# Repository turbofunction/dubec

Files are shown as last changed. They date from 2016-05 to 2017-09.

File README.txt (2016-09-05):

Contact:
Janne Savukoski
<firstname>@savukoski.name

                    Part name: DUBEC
                     Revision: 2.3
                   Board size: 40mm x 21.375mm
              Board thickness: 
                   Board type: Four layer
       Outer copper thickness:
       Inner copper thickness:
Solder mask color (top & bot):
 Silkscreen color (top & bot):

No special instructions.

Layer order:

TOP:    DUBEC.toplayer.ger
        DUBEC.internalplane1.ger
        DUBEC.internalplane2.ger
BOTTOM: DUBEC.bottomlayer.ger

Other files:

DUBEC.boardoutline.ger     Outline
DUBEC.topsoldermask.ger    Solder mask TOP
DUBEC.bottomsoldermask.ger Solder mask BOTTOM
DUBEC.topsilkscreen.ger    Silkscreen TOP
DUBEC.bottomsilkscreen.ger Silkscreen BOTTOM
DUBEC.drills.xln           Excellon drill
DUBEC.drl                  Drill rack
DUBEC.tcream.ger           Solder stencil (TOP)

Thank you!

Regards,
Janne Savukoski

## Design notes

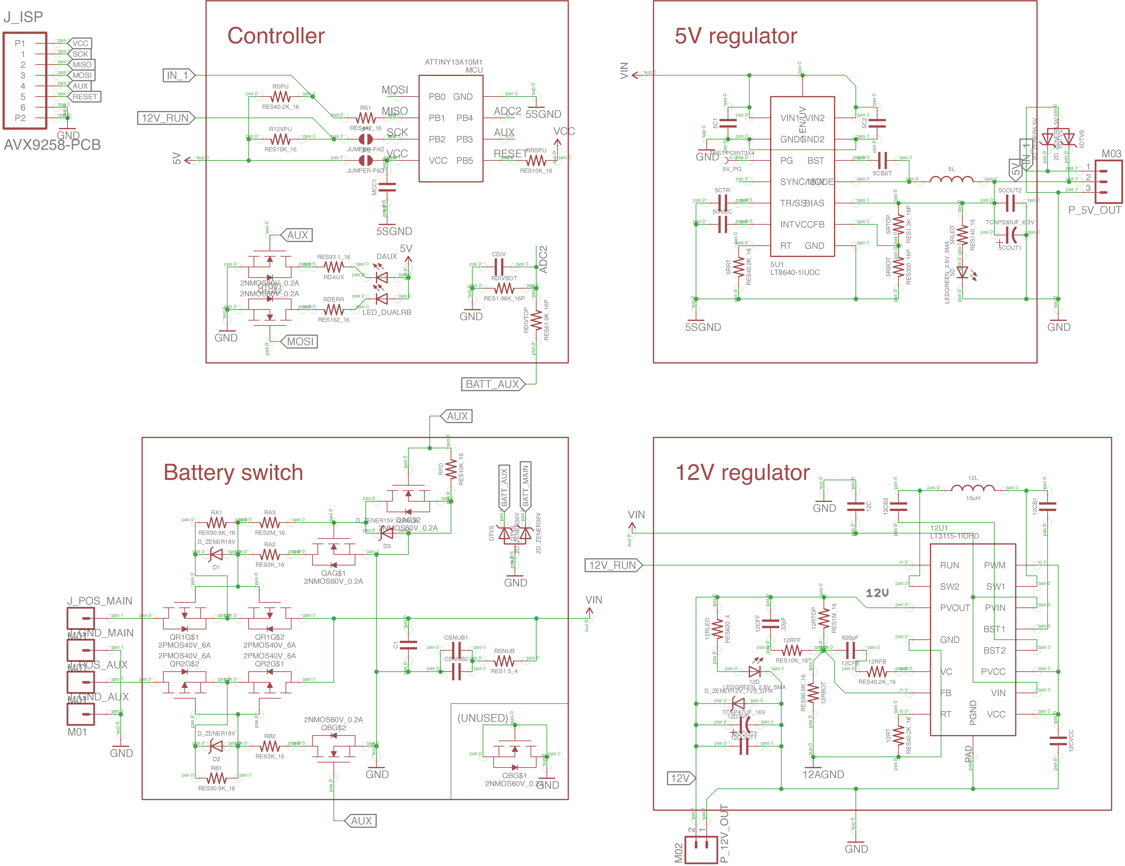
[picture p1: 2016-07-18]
DUBEC-schema-v2_0.png

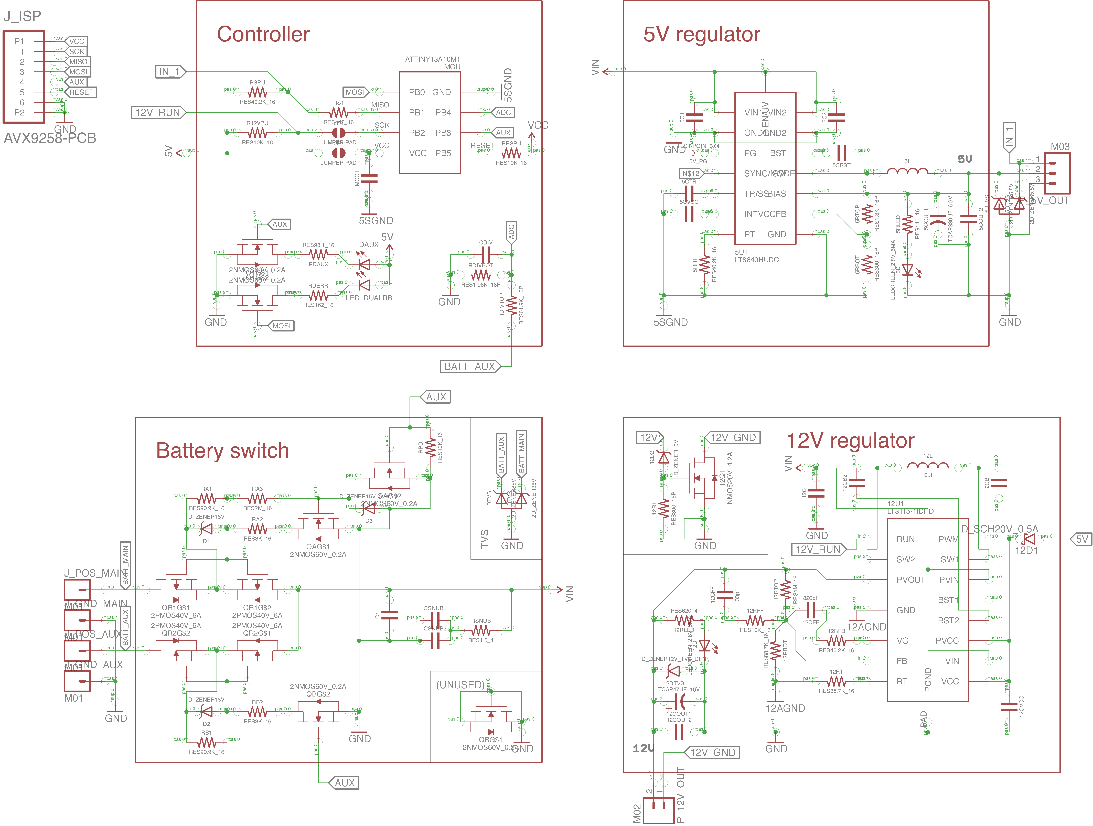
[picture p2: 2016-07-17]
DUBEC-schema.png

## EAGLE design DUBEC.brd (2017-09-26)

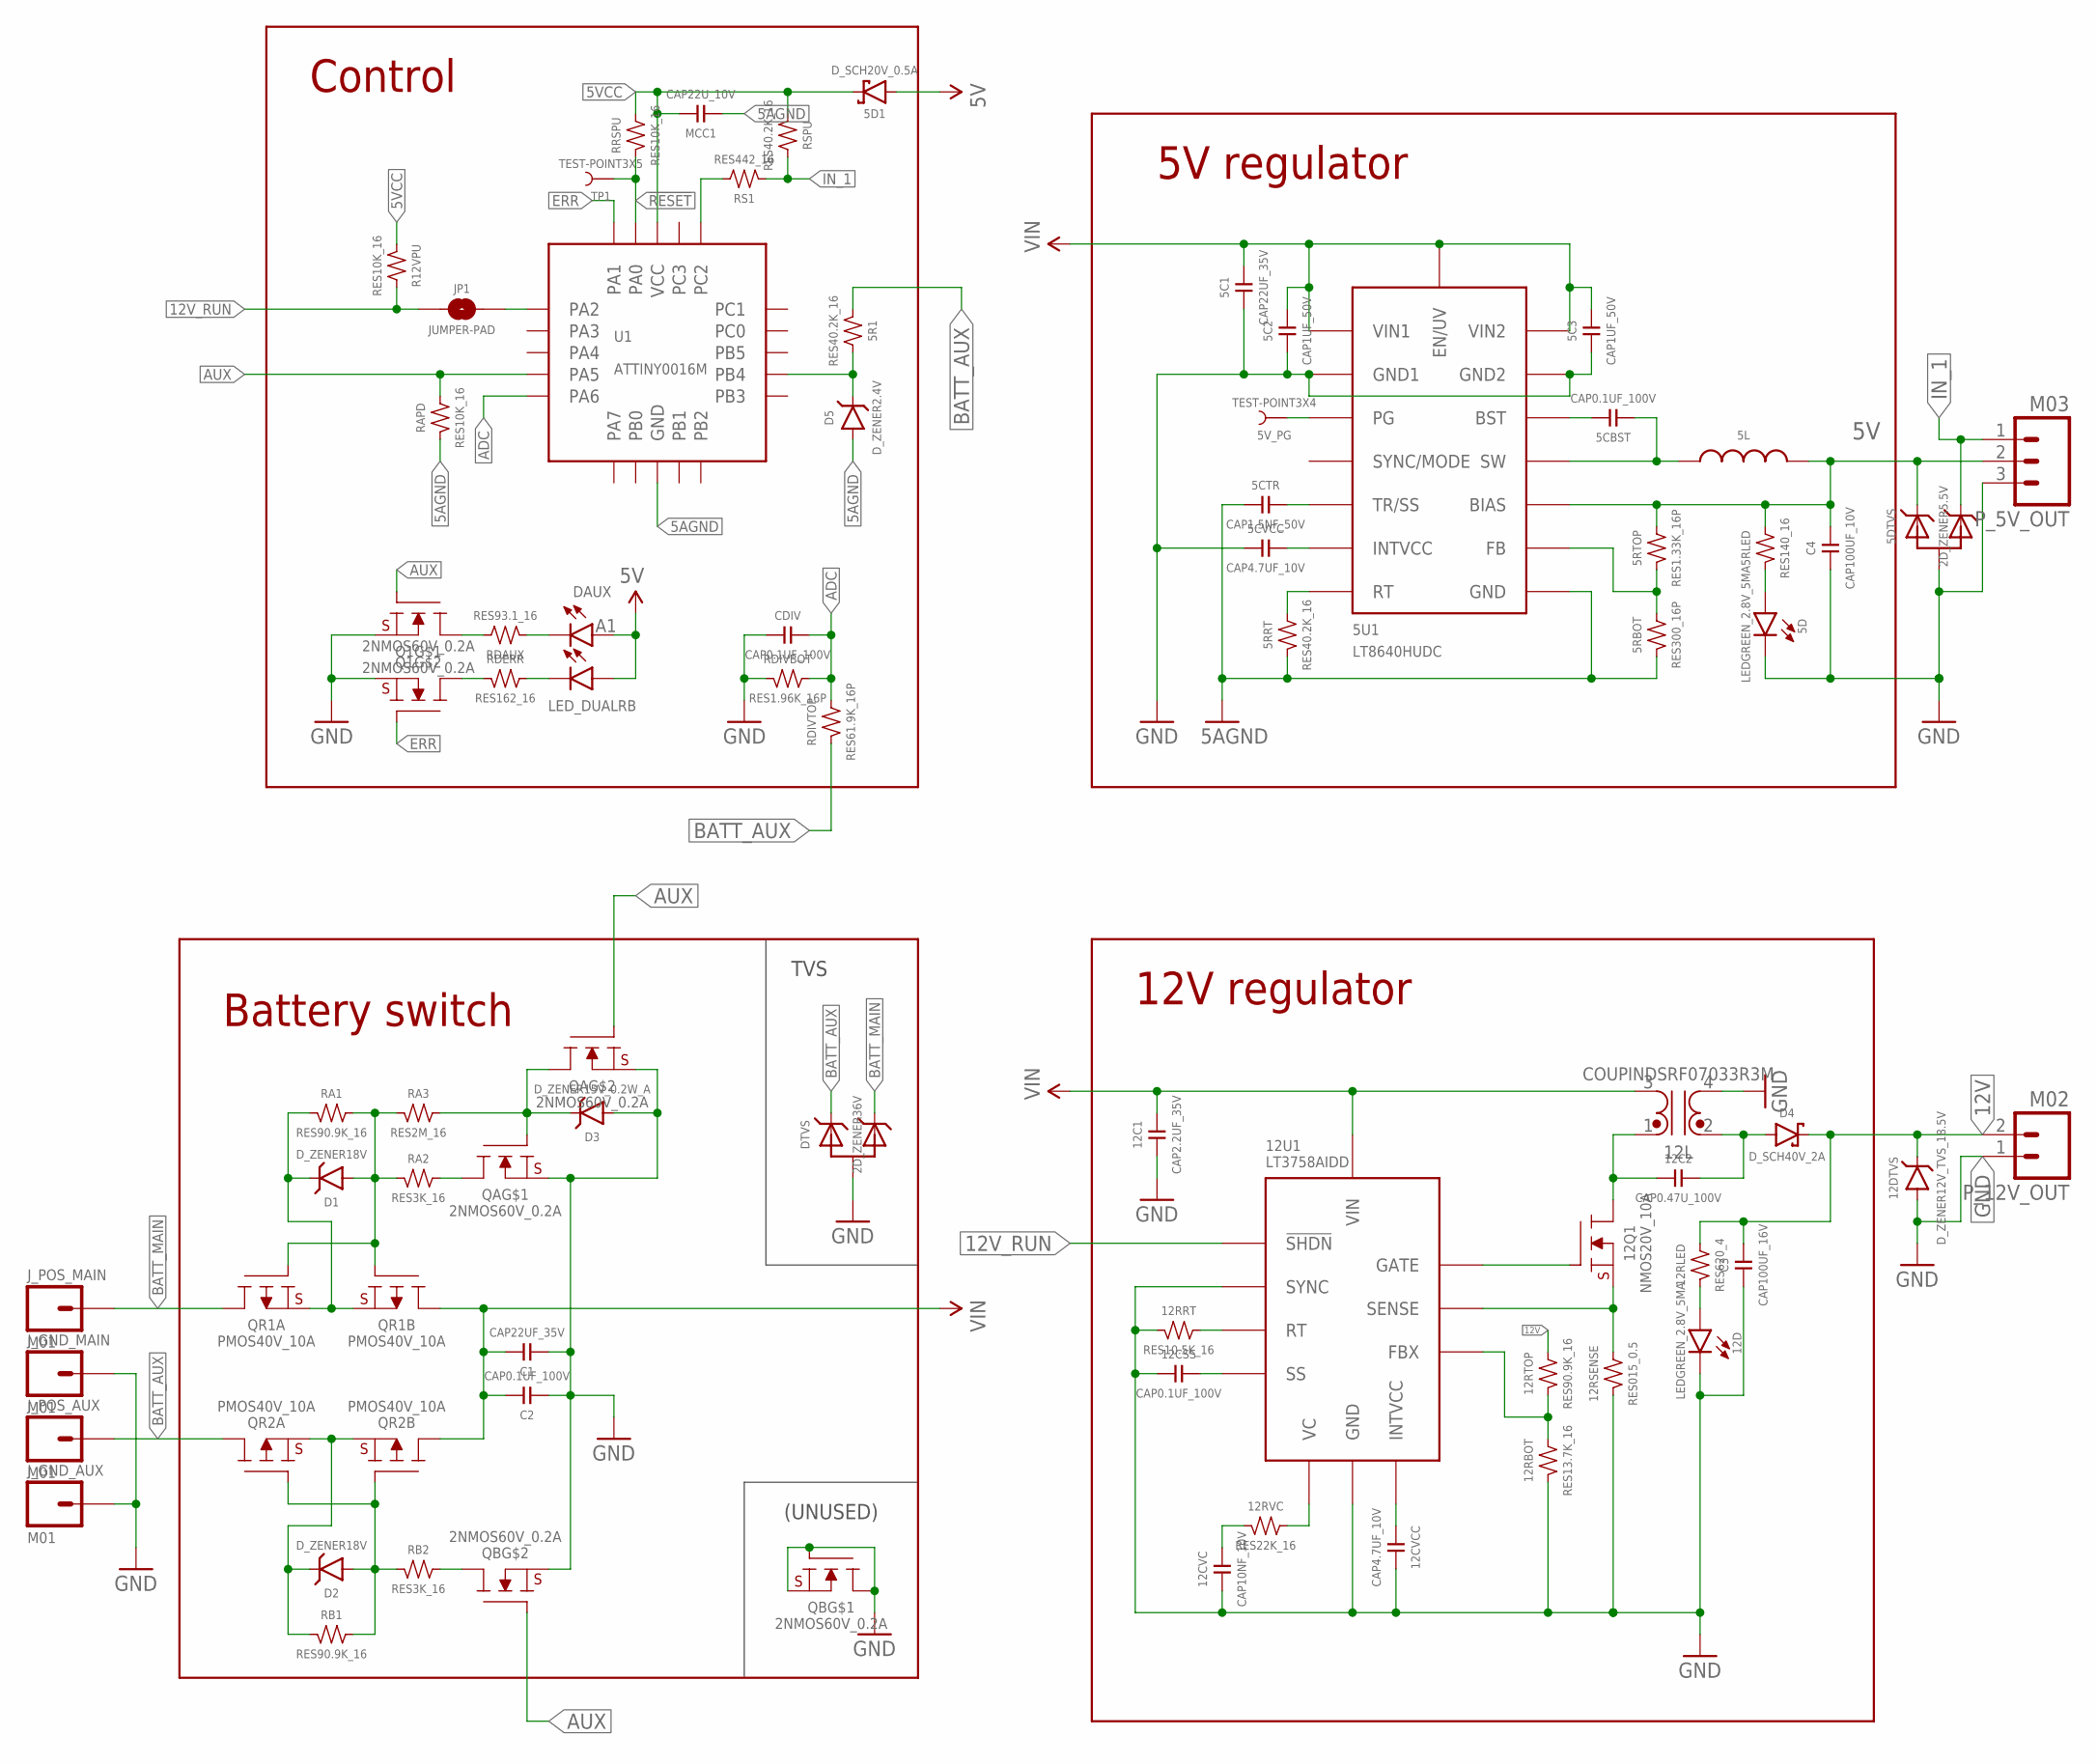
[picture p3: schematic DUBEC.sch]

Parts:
5C1: CAP22UF_35V; 0805
5C2, 5C3: CAP1UF_50V; 0603
5CBST, 12CSS: CAP0.1UF_100V; 0402
5CTR: CAP1.5NF_50V; 0402
5CVCC, 12CVCC: CAP4.7UF_10V; 0402
5D, 12D: LEDGREEN_2.8V_5MA; 0603+
5D1: D_SCH20V_0.5A; SOD523+
5DTVS: 2D_ZENER5.5V; SOT23-3
5L: I3.3UH_5A; SRP5030
5R1, 5RRT: RES40.2K_16; 0402
5RBOT: RES300_16P; 0402
5RLED: RES140_16; 0402
5RTOP: RES1.33K_16P; 0402
5U1: LT8640HUDC; QFN-18
5V_PG: TEST-POINT3X4; PAD.03X.04
12C1: CAP2.2UF_35V; 0402
12C2: CAP0.47U_100V; 0805
12CVC: CAP10NF_10V; 0402
12DTVS: D_ZENER12V_TVS_18.5V; SOD323+
12L: COUPINDSRF07033R3M; SRF0703
12Q1: NMOS20V_10A; 6-PQFN
12RBOT: RES13.7K_16; 0402
12RLED: RES620_4; 0603
12RRT: RES10.5K_16; 0402
12RSENSE: RES015_0.5; 1206
12RTOP: RES90.9K_16; 0402
12RVC: RES22K_16; 0402
12U1: LT3758AIDD; DFN-10
C1: CAP22UF_35V; 0805
C2: CAP0.1UF_100V; 0402
C3: CAP100UF_16V; 1210
C4: CAP100UF_10V; 1210
CDIV: CAP0.1UF_100V; 0402
D1, D2: D_ZENER18V; SOD523+
D3: D_ZENER15V_0.2W_A; SOD523+
D4: D_SCH40V_2A; DO-214AC
D5: D_ZENER2.4V; SOD523+
DAUX: LED_DUALRB; 0603+DUAL
DTVS: 2D_ZENER36V; SOT23-3
JP1: JUMPER-PAD; JUMPER-PAD-ROUND
J_GND_AUX: M01; 1X01_NO_SILK
J_GND_MAIN: M01; 1X01_NO_SILK
J_POS_AUX: M01; 1X01_NO_SILK
J_POS_MAIN: M01; 1X01_NO_SILK
MCC1: CAP22U_10V; 0603
P_5V_OUT: M03; 1X03_NO_SILK
P_12V_OUT: M02; 1X02_NO_SILK
Q1: 2NMOS60V_0.2A; SOT-666
QA: 2NMOS60V_0.2A; SOT-666
QB: 2NMOS60V_0.2A; SOT-666
QR1A, QR1B, QR2A, QR2B: PMOS40V_10A; POWERDI3333-8
R12VPU: RES10K_16; 0402
RA1: RES90.9K_16; 0402
RA2: RES3K_16; 0402
RA3: RES2M_16; 0402
RAPD: RES10K_16; 0402
RB1: RES90.9K_16; 0402
RB2: RES3K_16; 0402
RDAUX: RES93.1_16; 0402
RDERR: RES162_16; 0402
RDIVBOT: RES1.96K_16P; 0402
RDIVTOP: RES61.9K_16P; 0402
RRSPU: RES10K_16; 0402
RS1: RES442_16; 0402
RSPU: RES40.2K_16; 0402
TP1: TEST-POINT3X5; PAD.03X.05
U1: ATTINY0016M; 20-VQFN-2

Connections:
5AGND: 5CTR.1, 5RBOT.1, 5RRT.1, 5U1.18 (GND), D5.A, MCC1.1, RAPD.1, U1.3 (GND), U1.PAD (GND)
5V: 5D1.A, 5DTVS.1 (C1), 5L.2, 5RLED.2, 5RTOP.2, 5U1.1 (BIAS), C4.2, DAUX.A1, DAUX.A2, P_5V_OUT.2
5VCC: 5D1.C, MCC1.2, R12VPU.1, RRSPU.2, RSPU.1, U1.4 (VCC)
5V_BST: 5CBST.2, 5U1.3 (BST)
5V_FB: 5RBOT.2, 5RTOP.1, 5U1.20 (FB)
5V_PG: 5U1.19 (PG), 5V_PG.P$1
5V_RT: 5RRT.2, 5U1.15 (RT)
5V_SW: 5CBST.1, 5L.1, 5U1.8-9 (SW), 5U1.21 (SW), 5U1.22 (SW)
5V_TR: 5CTR.2, 5U1.16 (TR/SS)
5V_VCC: 5CVCC.2, 5U1.2 (INTVCC)
12FBX: 12RBOT.2, 12RTOP.1, 12U1.2 (FBX)
12GATE: 12Q1.G, 12U1.7 (GATE)
12INTVCC: 12CVCC.1, 12U1.8 (INTVCC)
12RT: 12RRT.2, 12U1.4 (RT)
12SENSE: 12Q1.S, 12RSENSE.2, 12U1.6 (SENSE)
12SS: 12CSS.2, 12U1.3 (SS)
12V: 12DTVS.C, 12RLED.2, 12RTOP.2, C3.2, D4.C, P_12V_OUT.2
12VC: 12RVC.2, 12U1.1 (VC)
12V_RUN: 12U1.9 (!SHDN), JP1.1, R12VPU.2
!RESET: RRSPU.1, TP1.P$1, U1.19 (PA0)
ADC: CDIV.2, RDIVBOT.2, RDIVTOP.2, U1.7 (PA6)
AUX: Q1.2 (G), QA.5 (G), QB.5 (G), RAPD.2, U1.6 (PA5)
BATT_AUX: 5R1.1, DTVS.1 (C1), J_POS_AUX.1, QR2A.D, RDIVTOP.1
BATT_MAIN: DTVS.2 (C2), J_POS_MAIN.1, QR1A.D
ERR: Q1.5 (G), U1.20 (PA1)
GATE_AUX: D2.A, QR2A.G, QR2B.G, RB1.2, RB2.1
GATE_MAIN: D1.A, QR1A.G, QR1B.G, RA1.2, RA2.1, RA3.1
GATE_MAIN_B: D3.C, QA.2 (G), QA.3 (D), RA3.2
GND: 5C1.1, 5C2.1, 5C3.1, 5CVCC.1, 5D.C, 5DTVS.3 (A), 5U1.6 (GND1), 5U1.7 (GND1), 5U1.10 (GND2), 5U1.11 (GND2), 12C1.1, 12CSS.1, 12CVC.1, 12CVCC.2, 12D.C, 12DTVS.A, 12L.4 (B2), 12RBOT.1, 12RRT.1, 12RSENSE.1, 12U1.5 (SYNC), 12U1.PAD (GND), C1.1, C2.1, C3.1, C4.1, CDIV.1, D3.A, DTVS.3 (A), J_GND_AUX.1, J_GND_MAIN.1, P_5V_OUT.3, P_12V_OUT.1, Q1.1 (S), Q1.4 (S), QA.1 (S), QA.4 (S), QB.1 (S), QB.2 (G), QB.4 (S), QB.6 (D), RDIVBOT.1
IN_1: 5DTVS.2 (C2), P_5V_OUT.1, RS1.1, RSPU.2
LED_BLUE: Q1.6 (D), RDAUX.1
LED_RED: Q1.3 (D), RDERR.2
unnamed: 5R1.2, D5.C, U1.10 (PB4)
unnamed: 5D.A, 5RLED.1
unnamed: RS1.2, U1.17 (PC2)
unnamed: 12D.A, 12RLED.1
unnamed: DAUX.C1, RDAUX.2
unnamed: QA.6 (D), RA2.2
unnamed: QB.3 (D), RB2.2
unnamed: DAUX.C2, RDERR.1
unnamed: 12CVC.2, 12RVC.1
unnamed: 12C2.1, 12L.1 (A1), 12Q1.D
unnamed: 12C2.2, 12L.2 (B1), D4.A
unnamed: JP1.2, U1.1 (PA2)
SRC_AUX: D2.C, QR2A.S, QR2B.S, RB1.1
SRC_MAIN: D1.C, QR1A.S, QR1B.S, RA1.1
VIN: 5C1.2, 5C2.2, 5C3.2, 5U1.4 (VIN1), 5U1.13 (VIN2), 5U1.14 (EN/UV), 12C1.2, 12L.3 (A2), 12U1.10 (VIN), C1.2, C2.2, QR1B.D, QR2B.D

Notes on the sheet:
(UNUSED)
12V regulator
5V regulator
Battery switch
Control
TVS

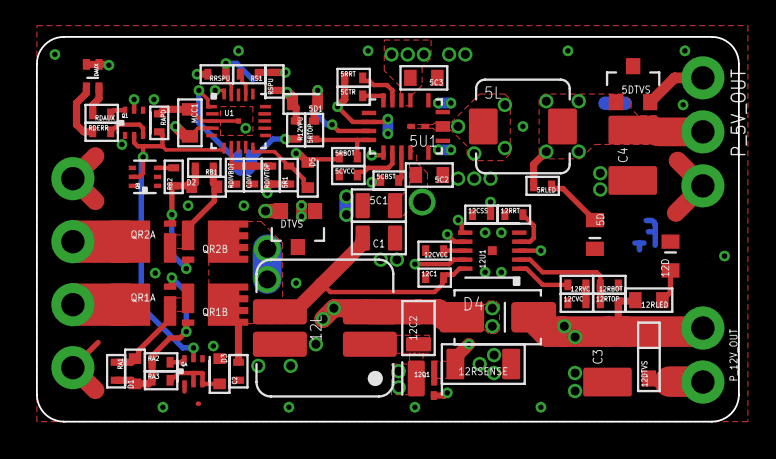
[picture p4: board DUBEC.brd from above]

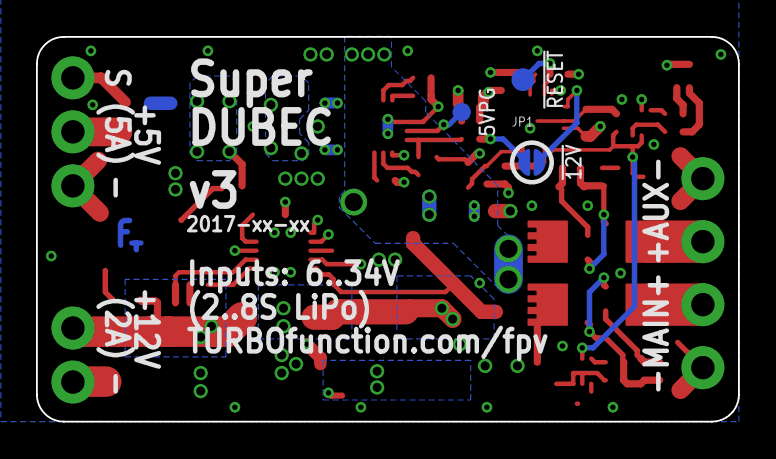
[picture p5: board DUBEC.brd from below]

Board: 4 copper layers, 39.0 x 21.4 mm, 77 parts (4 on the bottom side), 47 nets.

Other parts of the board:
U$1: TF-EMBLEM

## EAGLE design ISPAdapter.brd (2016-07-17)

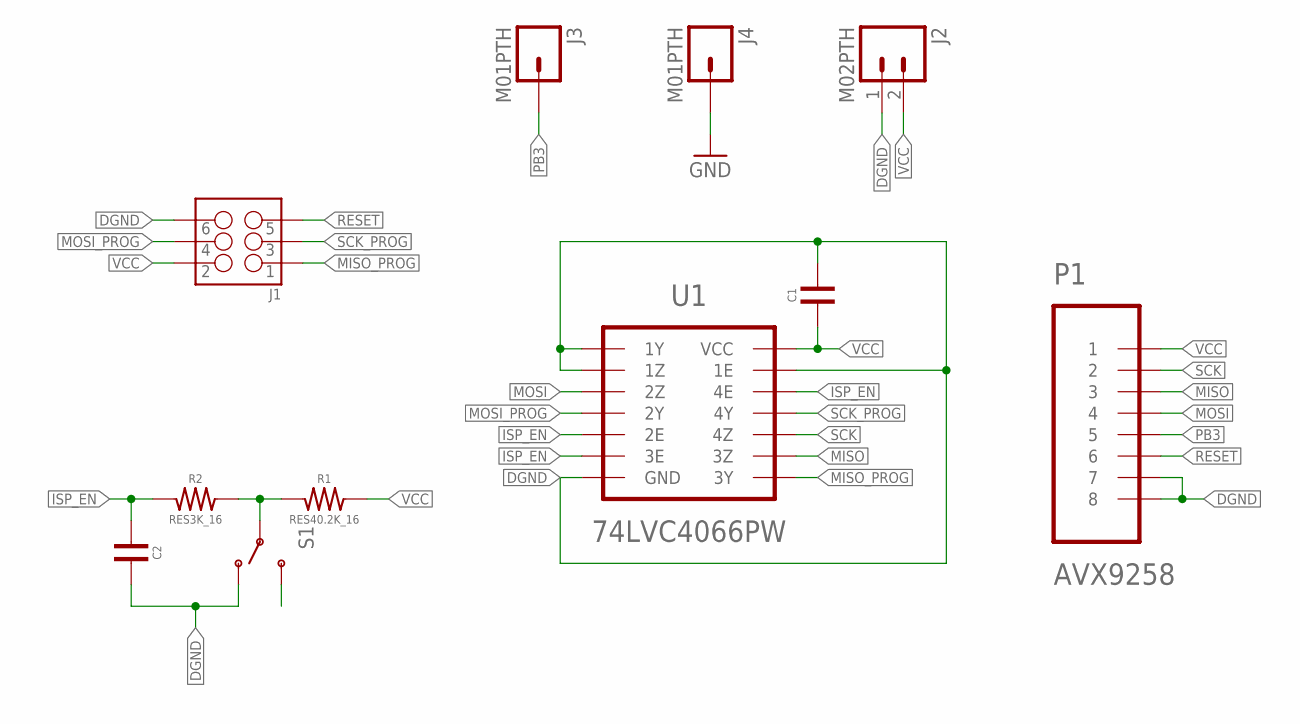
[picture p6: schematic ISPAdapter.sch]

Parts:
C1: CAP4.7UF_10V; 0402
C2: CAP0.1UF_100V; 0402
J1: M03X2WR; WR-BHD-3X2
J2: M02PTH; 1X02
J3, J4: M01PTH; 1X01
P1: AVX9258; AVX9258-8C
R1: RES40.2K_16; 0402
R2: RES3K_16; 0402
S1: SWITCH-SPDTESWITCH; EG1271A
U1: 74LVC4066PW; 14-TSSOP

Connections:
DGND: C1.2, C2.2, J1.6, J2.1, P1.7, P1.8, S1.1 (O), S1.4 (O), U1.1 (1Y), U1.2 (1Z), U1.7 (GND), U1.13 (1E)
GND: J4.1
ISP_EN: C2.1, R2.1, U1.5 (2E), U1.6 (3E), U1.12 (4E)
MISO: P1.3, U1.9 (3Z)
MISO_PROG: J1.1, U1.8 (3Y)
MOSI: P1.4, U1.3 (2Z)
MOSI_PROG: J1.4, U1.4 (2Y)
unnamed: S1.3 (S), S1.6 (S)
PB3: J3.1, P1.5
RESET: J1.5, P1.6
SCK: P1.2, U1.10 (4Z)
SCK_PROG: J1.3, U1.11 (4Y)
SWGND: R1.1, R2.2, S1.2, S1.5
VCC: C1.1, J1.2, J2.2, P1.1, R1.2, U1.14 (VCC)

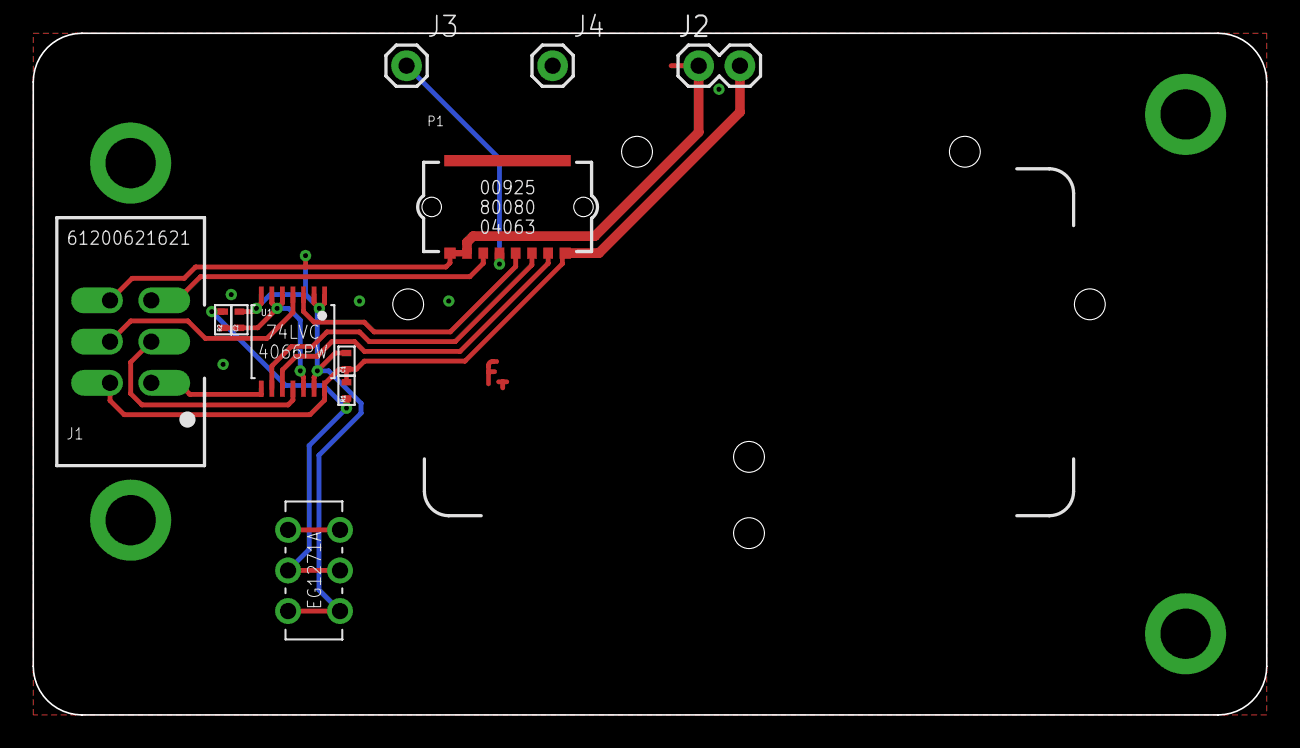
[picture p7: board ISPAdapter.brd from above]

Board: 2 copper layers, 76.0 x 42.0 mm, 12 parts (0 on the bottom side), 13 nets.

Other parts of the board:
U$2: TF-EMBLEM

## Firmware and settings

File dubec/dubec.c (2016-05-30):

/**
 * dubec.c
 *
 * RC battery switch firmware for DUBEC, a dual voltage
 * regulator circuit.
 *
 * Created: 10/3/2014 2:16:55 AM
 * Author: janne@turbofunction.com
 */

#include <avr/io.h>
#include <avr/power.h>
#include <avr/sleep.h>
#include <avr/wdt.h>
#include <util/atomic.h>

#define TRUE 1
#define FALSE 0

// red LED
#define PIN_AUX_NOT_BAD PORTB0
// RC signal input
#define PIN_SIG PORTB1
// 12V regulator on/off
#define PIN_12V PORTB2
// FET gate net (and green LED)
#define PIN_BATT_SWITCH PORTB3
// AUX battery voltage divider net
#define PIN_ADC PORTB4

// range with 61.9k/1.96k divider: [6..33.6V] -> [0.190..1.06V]
// -9 is calibration
#define MIN_VOLTAGE ((uint16_t) (6 / 33.6 * 1024 - 9))

// switch between main and AUX battery
#define batt_main() { PORTB &= ~_BV(PIN_BATT_SWITCH); }
#define batt_aux() { PORTB |= _BV(PIN_BATT_SWITCH); }

// hi-z the line to allow it to get pulled high
#define enable_12V() { DDRB &= ~_BV(PIN_12V); }
// pull line low by enabling output
#define disable_12V() { DDRB |= _BV(PIN_12V); }

#define warn_on() { PORTB |= _BV(PIN_AUX_NOT_BAD); }
#define warn_off() { PORTB &= ~_BV(PIN_AUX_NOT_BAD); }
#define warn_toggle() { PORTB ^= _BV(PIN_AUX_NOT_BAD); }

// evaluates to true if waiting for high RC signal
#define is_trigger_high() (MCUCR & (_BV(ISC01) | _BV(ISC00)))

// evaluates to true if timer is counting
#define is_timer_running() (TCCR0B)

// configure watchdog with the given prescaler
#define watchdog(wdtp) ({ ATOMIC_BLOCK(ATOMIC_RESTORESTATE) { WDTCR = _BV(WDCE); WDTCR = wdtp; } WDTCR |= _BV(WDTIE); })

// Enable ADC and ADC interrupt, conversion will
// start automatically on noise reduction sleep.
#define start_ADC() { ADCSRA |= _BV(ADIE) | _BV(ADSC); }

#define MIN(a, b) (a < b ? a : b)
#define MAX(a, b) (a < b ? b : a)

// AUX battery is depleted
#define AUX_BAD 1
// AUX is low
#define AUX_WARN 2
// self-explanatory
#define AUX_OK 3

typedef struct {
	// see AUX_*
	uint8_t aux_status;
	/**
	 * Watchdog/ADC is set to to higher rate to detect
	 * battery disconnect faster, but warning blink
	 * is 1Hz (ie., 0.5s toggle). And I decided to
	 * sample battery also at that slower rate.
	 * (So, store only every so manyeth sample.)
	 */
	uint8_t until_sample;
	/**
	 * Fallback level is set to 75% of measured initial voltage
	 * level, ie. 4.2V results in 3.15V and 3.8V makes 2.85V.
	 * Thus, if you rely on the device to not allow battery to
	 * discharge down to 2.85V, make sure that the initial charge
	 * is a lot more than 3.8V (per cell).
	 *
	 * Note: There's a(n incomplete) version in history with
	 * cell count detection, but it didn't feel to be significantly
	 * better. (Better as in avoiding unnecessary fallbacks versus
	 * killing batteries.) And, to keep in mind, I intend to use this
	 * with my own batteries as well.
	 *
	 * Rule: Don't launch with a drained battery!
	 */
	uint16_t fallback_voltage;
	// when to start flashing warning LED
	uint16_t warn_voltage;
	// battery voltage sample memory
	uint16_t samples[3];
} battery_t;

// http://embeddedgurus.com/barr-code/2012/11/how-to-combine-volatile-with-struct/
// also: initializing to zero, just to avoid thinking
// that "this variable can't have an unknown value"
battery_t volatile batt = { 0, 9, 0, 0, { 0 } };

// sourcing from main battery
#define SIG_MAIN 1
// sourcing from AUX battery
#define SIG_AUX 2
// crash boom bang. also switch to main battery.
#define SIG_12V_DISABLE 3

// mapping from signal level to state
#define SIG_LOW SIG_MAIN
#define SIG_MID SIG_AUX
#define SIG_HIGH SIG_12V_DISABLE

typedef struct {
	// the raw timing value from interrupt handler
	uint8_t pwm;
	// see SIG_*
	uint8_t status;
	// user is switching into a different mode,
	// to be applied after counter
	uint8_t pending;
	// countdown to applying status change
	uint8_t until_flip;
} rc_signal_t;

rc_signal_t volatile signal = { 0, 0, 0, 0 };

static void process_signal(void);

static void process_voltage(void);

static void apply_state(void);

static void set_aux(uint8_t aux_status);


int main(void) {
	/**
	 * Pin configuration:
	 *
	 * PB0 (MOSI):
	 *   red LED (bad AUX voltage) output; low-side, inverted
	 * PB1 (AIN1, PCINT1, INT0, MISO):
	 *   RC signal digital input, external pull-up
	 * PB2 (SCK):
	 *   12V run output, external pull-up
	 * PB3 (ADC3):
	 *   battery switch & AUX LED output, external pull-down
	 * PB4 (ADC2, PCINT4):
	 *   AUX battery voltage (divider) input, pulled down naturally if no battery
	 * PB5 (RESET):
	 *   input with external pull-up, connected only to ISP
	 */

	// configure outputs
	DDRB = _BV(PIN_BATT_SWITCH) | _BV(PIN_AUX_NOT_BAD);

	// disable all digital inputs
	DIDR0 = 0b111111;

	// configure ADC to read PB4, and reference to internal 1.1V
	ADMUX = _BV(MUX1) | _BV(REFS0);

	// Enable level interrupt. INT0 is triggered on low
	// by default, which is the correct mode initially (pin
	// pulled high externally).
	GIMSK = _BV(INT0);

	// enable timer counter overflow interrupt
	TIMSK0 = _BV(TOIE0);

	// Configure ADC clock to 75kHz (1.2MHz / 16).
	// (Must be 50..200kHz.)
	ADCSRA = _BV(ADEN) | _BV(ADPS2);

	// global interrupt enable, SREG |= SREG_I
	sei();

	watchdog(WDTO_60MS);

	// Trigger first ADC only after the first watchdog timeout
	// to allow initializations. (Unsure whether the CPU power down
	// cancels all that, though.) Thus, commented out:
	//start_ADC();

	for (;;) {
		process_signal();
		process_voltage();

		// configure sleep according to state

		if (is_timer_running()) {
			// idle when timing high signal to keep IO clock running (for timer)
			MCUCR &= ~(_BV(SM0) | _BV(SM1)); // idle

		} else if (bit_is_set(ADCSRA, ADIE)) {
			// ADC is pending, conversion will start automatically with sleep.
			// Note that this will inhibit high signal tracking on INT0,
			// but the conversion should be finished well before the next rise.
			MCUCR = (MCUCR & ~_BV(SM1)) | _BV(SM0); // ADC noise reduction

		} else if (is_trigger_high()) {
			// ~18ms wait period on low signal, sleep or not? If we just idle
			// for now to avoid risks.. (Thus, configured now to use synchronous
			// INT0 on signal instead of async PCINT; easier interrupt handling.)
			MCUCR &= ~(_BV(SM0) | _BV(SM1)); // idle

		} else {
			// Set sleep mode to power down, watchdog or pin change
			// interrupt will wake up.
			MCUCR = (MCUCR & ~_BV(SM0)) | _BV(SM1); // power down
		}

		sleep_cpu();
	}
}


static void process_signal(void) {
	// take a local (non-volatile) copy
	uint8_t pwm = signal.pwm;

	if (!pwm) {
		return;
	}

	// flag as read
	signal.pwm = 0;

	// accepted range [800..2240ms] == [15..42] @ 18.75kHz
	if (pwm < 15 || pwm > 42) {
		// invalid signal, reset counter
		if (signal.until_flip) {
			signal.until_flip = 5;
		}
		return;
	}

	// [800..1333ms[
	uint8_t want = SIG_LOW;
	if (pwm > 32) {
		// ]1653..2240ms]
		want = SIG_HIGH;
	} else if (pwm >= 25) {
		// [1333..1653ms]
		want = SIG_MID;
	}

	if (want == signal.pending) {
		if (signal.until_flip) {
			if (!--signal.until_flip) {
				signal.status = signal.pending;
				apply_state();
			}
		} // else the change is already applied
	} else {
		signal.pending = want;
		signal.until_flip = 5;
	}
}


static void process_voltage(void) {
	// take a local (non-volatile) copy
	uint16_t samples[3] = { batt.samples[0], batt.samples[1], batt.samples[2] };

	if (!samples[0]) {
		return;
	}

	// rotate the sample memory and flag as processed
	batt.samples[2] = samples[1];
	batt.samples[1] = samples[0];
	batt.samples[0] = 0;

	uint16_t v_max = MAX(samples[0], MAX(samples[1], samples[2]));

	if (v_max < (MIN_VOLTAGE >> 1)) {
		set_aux(AUX_BAD);
		/**
		 * Need to be careful when reseting the fallback
		 * voltage, so that it won't get reseted when
		 * there's eg. some sudden voltage ripple/sag
		 * due to a transient load.
		 *
		 * This is ensured now by checking that all the
		 * ADC samples are low.
		 */
		batt.fallback_voltage = 0;
		batt.warn_voltage = 0;
		return;

	} else if (samples[0] < (MIN_VOLTAGE >> 1)) {
		// possibly battery disconnect
		start_ADC();
		return;
	}

	// All samples are now checked to be significantly non-zero,
	// next step is to check that they're somewhat stable.
	// (All within 66mV.)
	uint8_t v_diff = v_max - MIN(samples[0], MIN(samples[1], samples[2]));
	if (v_diff > 2) {
		// defer any action if voltage is unstable
		return;
	}

	uint16_t v_avg = (samples[0] + samples[1] + samples[2]) / 3;

	if (v_avg < MIN_VOLTAGE) {
		set_aux(AUX_BAD);

	} else if (!batt.fallback_voltage) {
		// Fallback at 75% of voltage (3.15V for 4.2V);
		// floor the range, just for kicks.
		batt.fallback_voltage = MAX(v_avg - (v_avg >> 2), MIN_VOLTAGE);
		// Warning at 80% (3.36V for 4.2V). The division takes up
		// serious space, TODO optimize.
		batt.warn_voltage = (v_avg << 2) / 5;
		// wait for at least one more round until considering ok

	} else if (v_avg <= batt.fallback_voltage) {
		set_aux(AUX_BAD);

	} else if (v_avg <= batt.warn_voltage) {
		set_aux(AUX_WARN);

	// some hysteresis to prevent oscillation
	} else if (v_avg > (batt.warn_voltage + 1)) {
		set_aux(AUX_OK);

	// Don't get stuck on initial bad status. Could combine with
	// above, but more clear this way. Also, setting to OK instead
	// of warning -- even if it's just by a hair -- to respect
	// the calculated warning voltage level.
	} else if (!batt.aux_status || batt.aux_status == AUX_BAD) {
		set_aux(AUX_OK);
	}
}


static void apply_state(void) {
	// apply signal status first
	switch (signal.status) {
		case SIG_AUX:
			if (batt.aux_status >= AUX_WARN) {
				batt_aux();
				enable_12V();
				break;
			}
			// else fall through

		case SIG_MAIN:
		default:
			batt_main();
			enable_12V();
			break;

		case SIG_12V_DISABLE:
			// crashboombang-mode
			batt_main();
			disable_12V();
			break;
	}

	// then set also the LED state
	switch (batt.aux_status) {
		case AUX_OK:
			warn_off();
			break;

		case AUX_WARN:
			// let the ADC interrupt handler blink at its own rate
			break;

		case AUX_BAD:
		default:
			warn_on();
			break;
	}
}


static void set_aux(uint8_t aux_status) {
	if (batt.aux_status != aux_status) {
		batt.aux_status = aux_status;
		apply_state();
	}
}


/** RC signal handler. */
ISR(INT0_vect) {
	// Act based on trigger conf as PINB might already have flipped back. (And
	// the digital input is disabled anyways, due to this.)
	if (is_trigger_high()) {
		// Line is high, start timing the high period.

		// reset timer counter
		TCNT0 = 0;
		// set timer clock source to 1.2MHz/64 == 18.75kHz,
		// 2.2ms / 18.75Hz == 41.25
		TCCR0B = _BV(CS01) | _BV(CS00);
		// configure next interrupt on low
		MCUCR &= ~(_BV(ISC01) | _BV(ISC00));

	} else {
		// store counter value
		signal.pwm = TCNT0;
		// stop timer (after copying the value, to avoid surprises)
		TCCR0B = 0;
		// next interrupt on rising edge
		MCUCR |= _BV(ISC01) | _BV(ISC00);
	}
}


/** Stop timer on invalid RC signal. */
ISR(TIM0_OVF_vect) {
	// phase too long, stop timer
	TCCR0B = 0;
	// also reset counter in case it's been incrementing
	// during this interrupt handler (n00b doesn't know)
	TCNT0 = 0;
}


/**
 * Process battery voltage. Handles also bad AUX warning
 * LED blinking.
 */
ISR(ADC_vect) {
	// documentation states that the low byte needs to be read first
	uint16_t v = ADCL;
	// thus, read the high byte on a separate line to "ensure" proper ordering
	v |= ADCH << 8;

	// disable ADC interrupt
	ADCSRA &= ~_BV(ADIE);

	// either reached sampling time, or maybe battery disconnect
	if (v < (MIN_VOLTAGE >> 1) || !--batt.until_sample) {
		// at least 1 to flag the memory as unprocessed
		batt.samples[0] = MAX(v, 1);

		if (!batt.until_sample) {
			if (batt.aux_status == AUX_WARN) {
				// blink the red LED at 1Hz as a warning
				warn_toggle();
			}
			batt.until_sample = 9;
		}
	}
}


/**
 * Use watchdog to initiate AUX battery voltage check on regular intervals.
 */
ISR(WDT_vect) {
	start_ADC();
}

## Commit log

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2014-10-05 TPI isolation, relay diode
    [DUBEC.brd, DUBEC.sch]
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2014-10-05 Hacked in the supercap
    [DUBEC.brd, DUBEC.sch]
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2014-10-05 Recommended inductor for 5V
    [DUBEC.brd, DUBEC.sch]
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2014-10-07 Switch to ATtiny13A (EEPROM)
    [DUBEC.brd, DUBEC.sch]
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2014-10-14 Schematic fixes
    [DUBEC.brd, DUBEC.sch]
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2014-10-15 Wired AUX to ADC
    [DUBEC.brd, DUBEC.sch]
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2014-10-21 Bridge solution, diode 5V supercap to 12V
    [DUBEC.brd, DUBEC.sch]
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2014-10-25 Optimized voltage divider resistors
    [DUBEC.brd, DUBEC.sch]
2014-11-04 Problematic relay downgrade to 2A due to non-stock
    [DUBEC.brd, DUBEC.sch]
2014-11-04 Revert to gullwing, incomplete
    [DUBEC.brd, DUBEC.sch]
2014-11-04 Gullwing revert complete
    [DUBEC.brd]
2014-11-10 Alum cap instead of super cap
    [DUBEC.brd, DUBEC.sch]
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2014-11-15 Removed some ground vias
    [DUBEC.brd]
2014-11-23 SCR; won't work
    [DUBEC.brd, DUBEC.sch]
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2014-11-26 Moved relay control line off MOSI
    [DUBEC.brd, DUBEC.sch]
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2014-12-07 Increased switching frequencies to compensate small inductors
    [DUBEC.brd, DUBEC.sch]
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2014-12-10 5V reg conf updates
    [DUBEC.brd, DUBEC.sch]
2014-12-10 Switch to Simple Switcher
    [DUBEC.brd, DUBEC.sch]
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2014-12-11 Used space for a cap; tidying
    [DUBEC.brd, DUBEC.sch]
2014-12-12 Replaced final 0201 component
    [DUBEC.brd, DUBEC.sch]
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2015-01-02 Second 12V ceramic cap
    [DUBEC.brd, DUBEC.sch]
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2015-01-06 Port fixes; conf update to v1.1
    [dubec.c]
2015-01-06 FET mapping fix. fuck..
    [DUBEC.brd, DUBEC.sch]
2015-01-08 5V power diode upgrade (previous smoked)
    [DUBEC.brd, DUBEC.sch]
2015-01-08 A couple TVS diodes
    [DUBEC.brd, DUBEC.sch]
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2015-01-09 Relay to cut excess relay voltage
    [DUBEC.brd, DUBEC.sch]
2015-01-10 Bigger 5V power diode
    [DUBEC.brd, DUBEC.sch]
2015-01-11 Tidying, filled space with a cap
    [DUBEC.brd, DUBEC.sch]
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2015-01-15 Component & layout tweaks
    [DUBEC.brd, DUBEC.sch]
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2015-01-25 Voltage divider to 1.1V; component optimization; layout tweaks
    [DUBEC.brd, DUBEC.sch]
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2015-01-27 Test-fitting a couple pots
    [DUBEC.brd, DUBEC.sch]
2015-01-27 Revert "Test-fitting a couple pots"
    This reverts commit 098d1195ccc5a94882651b758a5cc31df5305fd6.
    [DUBEC.brd, DUBEC.sch]
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2015-02-09 Post-meltdown upgrades: Beefy TVS diode, relay wiring.
    [DUBEC.brd, DUBEC.sch]
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2015-02-11 Tweaked a few land patterns
    [DUBEC.brd, DUBEC.sch]
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2015-02-28 Relay resistor fix
    [DUBEC.brd, DUBEC.sch]
2015-03-01 Dedicated resistor for AUX testpoint
    [DUBEC.brd, DUBEC.sch]
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2015-04-13 Relay resistor update; cream tweaks
    [DUBEC.brd, DUBEC.sch]
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2015-04-19 Switch to MOSFET "relay"
    [DUBEC.brd, DUBEC.sch]
2015-04-19 Fixed one schematic error
    [DUBEC.brd, DUBEC.sch]
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2015-04-28 Tidying; cap package; LED resistor update
    [DUBEC.brd, DUBEC.sch]
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2015-05-13 Solder jump for 12v run
    [DUBEC.brd, DUBEC.sch]
2015-10-25 Drafting small ISP header
    [DUBEC.brd, DUBEC.sch]
2015-10-29 Wired new ISP pads
    [DUBEC.brd, DUBEC.sch]
2015-10-31 Restored output bypass caps
    [DUBEC.brd, DUBEC.sch]
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2015-11-02 Grounded screw holes; disconnected unused connector pins
    [ISPAdapter.brd, ISPAdapter.sch]
2015-11-02 Gate bias from source
    [DUBEC.brd, DUBEC.sch]
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2015-11-05 Voltage divider to 4.6V
    [DUBEC.brd, DUBEC.sch]
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2015-11-05 Reset pull-up
    [DUBEC.brd, DUBEC.sch]
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2015-11-13 IN pull-down instead of pull-up
    [DUBEC.brd, DUBEC.sch]
2015-11-13 Revert "IN pull-down instead of pull-up"
    This reverts commit 7647d503c6cdeac1e35f886be3c611ab72df0953.
    [DUBEC.brd, DUBEC.sch]
2015-11-16 IN pull-up fix
    [DUBEC.brd, DUBEC.sch]
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2015-11-18 Emblem to library; tweaks
    [DUBEC.brd, ISPAdapter.brd]
2015-11-18 AUX divider update (due to non-stock)
    [DUBEC.brd, DUBEC.sch]
2015-11-18 Firmware ADC fix
2015-11-20 Board fixes and isolation
    [DUBEC.brd]
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2015-11-24 More proper kelvining. Better be stable now...
    [DUBEC.brd]
2015-11-24 Kelvinized 5V as well
    [DUBEC.brd, DUBEC.sch]
2015-11-25 Removed too small mask stop elements
    [DUBEC.brd, DUBEC.sch]
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2015-11-26 Upped LED currents to 15mA
    [DUBEC.brd, DUBEC.sch]
2015-11-26 Fault LED wiring update
    [DUBEC.brd, DUBEC.sch]
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2015-12-01 Fixes to voltage average handling
    [dubec.c]
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2015-12-04 Noob bugfix; signal level mapping
    [dubec.c]
2015-12-04 Bugfix revert; I misread the assembler, it was correct after all. Also, let the compiler calculate the MIN_VOLTAGE.
    [dubec.c]
2015-12-06 Separate connector mounting pad
    [ISPAdapter.brd]
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2015-12-08 Added PB3 (AUX) to header for HVSP; adjusted LED resistors
    [DUBEC.brd, DUBEC.sch, ISPAdapter.brd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]
2015-12-08 Angled diodes, TODO snubber-RC
    [DUBEC.brd, DUBEC.sch]
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2015-12-13 NMOS to replace diode
    [DUBEC.brd, DUBEC.sch]
2015-12-13 Revert "NMOS to replace diode"
    This reverts commit b5f679a1d9c1df25f2a9366656623a2bb0e6c105.
    [DUBEC.brd, DUBEC.sch]
2015-12-13 Replaced diode with a solder pad
    [DUBEC.brd, DUBEC.sch]
2015-12-13 Pin change at 2.5V, can't use for battery detection. Thus, ADC ref to 1.1V.
    [DUBEC.brd, DUBEC.sch]
2015-12-14 Adapter wiring to match DUBEC 1.5
    [ISPAdapter.brd, ISPAdapter.sch]
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2015-12-15 Full PCB pattern for connector
    [DUBEC.brd, DUBEC.sch]
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2015-12-16 Added cap to switch
    [ISPAdapter.brd, ISPAdapter.sch]
2015-12-16 Moved solder pad to bottom
    [DUBEC.brd]
2015-12-17 Layout updates, land pattern tweaks
    [DUBEC.brd, DUBEC.sch, ISPAdapter.brd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]
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2015-12-20 Jack/Plug refs; offset pads
    [DUBEC.brd, DUBEC.sch, ISPAdapter.brd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]
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2015-12-21 More consistent LED wiring
    [DUBEC.brd, DUBEC.sch]
2015-12-22 FET driver for status led
    [DUBEC.brd, DUBEC.sch]
2015-12-22 Status LED resistors; tidy
    [DUBEC.brd, DUBEC.sch]
2015-12-22 Status LED to 20mA
    [DUBEC.brd, DUBEC.sch]
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2016-02-24 5V regulator update; inductors from digikey
    [DUBEC.brd, DUBEC.sch]
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2016-02-26 5V configured to Forced Continuous mode
    [DUBEC.brd, DUBEC.sch]
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2016-02-28 Ground plane fix; tidy
    [DUBEC.brd]
2016-02-28 Restored MCU diode; couldn't recall any reason to avoid it now that using 1.1V as ADC reference
    [DUBEC.brd, DUBEC.sch]
2016-02-28 Dropped VCC jumper pad; cleanup
    [DUBEC.brd, DUBEC.sch]
2016-03-01 Corrected hole position
    [ISPAdapter.brd]
2016-03-01 Tidying based on proto
    [DUBEC.brd, DUBEC.sch]
2016-03-01 Moved hole and tightened dia to 1.9mm
    [ISPAdapter.brd, ISPAdapter.sch]
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2016-03-01 12V reg pad simplification and tweaks. Also to analog ground <- not sure if a good idead.
    [DUBEC.brd, DUBEC.sch]
2016-03-02 redo 12V reg pad mask & cream
    [DUBEC.brd, DUBEC.sch]
2016-03-08 DRC fixes; tidy
    [DUBEC.brd]
2016-03-08 Kelvin MCU to 5V ground
    [DUBEC.brd, DUBEC.sch]
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2016-03-16 Solder stencil fixes
    [ISPAdapter.brd]
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2016-03-25 Default set of visible layers
    [DUBEC.brd]
2016-03-25 Deja vu: replaced MCU diode with a jumper pad
    [DUBEC.brd, DUBEC.sch]
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2016-04-04 Draft: replace diodes with mosfets
    [DUBEC.brd, DUBEC.sch]
2016-04-05 Laying out the mosfet switch
    [DUBEC.brd, DUBEC.sch]
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2016-04-05 Replaced diodes with fets
2016-04-05 Excess board space? Drill a hole.
    [DUBEC.brd]
2016-04-05 Added spot for another snubber cap
    [DUBEC.brd, DUBEC.sch]
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2016-04-11 ADC divider now to 1.1V. Previous commit was the 5V divider...
    [DUBEC.brd, DUBEC.sch]
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2016-07-17 Loop fix, tweaks
    [DUBEC.brd]
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2016-07-19 Tiny fix
    [DUBEC.brd]
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2016-07-25 Package fix
    [DUBEC.brd, DUBEC.sch]
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2016-09-27 Solder stop margins, due to OSHPark reg error
    [DUBEC.brd, DUBEC.sch]
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2017-08-23 Rework finished?
    [DUBEC.brd, DUBEC.sch]
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2017-08-30 MOS type correction
    [DUBEC.brd, DUBEC.sch]
2017-08-31 Ok, keeping it safe.. (dropped the grounding of NC MCU pins)
    [DUBEC.brd, DUBEC.sch]

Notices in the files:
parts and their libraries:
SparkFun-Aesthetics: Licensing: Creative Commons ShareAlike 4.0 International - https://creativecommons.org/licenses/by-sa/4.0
